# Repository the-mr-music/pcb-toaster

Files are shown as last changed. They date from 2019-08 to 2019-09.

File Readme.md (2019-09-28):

# PCB Toaster



> **WARNING:** This project is dealing with 230VAC. You have to take safety preautions and provide proper isolation. Never touch the mains side of the circuit if power is applied. If you are not experienced in high voltage electronics do not attempt to build this circuit. I do take NO WARRANTY or LIABILITY for any damages when building or operating this device.

## Introduction

In my spare time I have been doing quite a lot of PCBs over the years. Starting with SMD sizes of 1206, with increasing circuit complexity I started using smaller and smaller component sizes. From 1206 over 0805, now ending up at 0402 and my first stenciling "adventures". Whilst browsing Instagram, I stumbled upon [Maker Moekoe's Hot Plate Reflow Iron](https://github.com/makermoekoe/Hotplate-Soldering-Iron), from which I grabbed a bit of inspiration for this quite similar project. As I did not have any spare parts lying around and wanted to do something with higher voltages anyway, I decided to build an all-in-one PCB.
(Fun fact - it is not actually a toaster)

## Roadmap

This current project is still work in progress. Be sure to check back later when it's finished.

- [x] Get an iron and disassemble it
- [x] Do all the calculations on the power side
- [x] Component selection
- [x] Design and order the PCB
- [x] Build and test the PCB
- [x] Plan the case and mounting, get materials
- [x] Take a nap
- [x] PCBs arrive 
- [x] Build and wire everything
- [x] Read up theoretical information about reflow soldering and solder paste
- [x] Program a first firmware version (curious if PID regulator will be necessary or a plain two-point regulator is sufficient)
- [ ] Refine the firmware

## PCB Design Notes

### Primary Side

Having only done one pcb incorporating 230 VAC and low voltage (before always used old 5 V phone chargers or other PSUs), but on serparate pcbs, I wanted to opt for an all-on-one pcb design. At LCSC.com I found an affordable print switching PSU ([GTL-POWER-VB02](https://datasheet.lcsc.com/szlcsc/1811211452_GTL-POWER-VB02-T2S03_C335526.pdf)), with an output of 3.3 V at 500 mA, which seemed perfect for the job. Their datasheet (at least the parts I could understand with the help of translator) recommended additional filtering at the output, which has been followed by me. Regarding the primary side, either a simple approach consisting out of a fuse, a varistor and a current limiting resistor or a more EMV saving pre-circuit is possible. As this device is just occasionally in use, the protective circuit is good enough for me.

Regarding the power switch for the iron itself, a BT-138 is used. Primarily because I already had this type of TRIAC already in use together with a MOC3083 and know it's working well together. The resistor values are taken from the MOC's datasheet. Because the SMD resistors have a maximum voltage rating of 250 V, I put two of them in series. All of the tracks carrying the heavy load are approximately five millimeters wide, but run on two layers. As a result a current of in total 10 A is achievable, which is limited by the fuse F1. For ease of layouting, the psu (on fuse F2) and iron are sharing F1. As the iron I use has a cold resistance of 42 Ohms, a 6.3 Ampere fuse is sufficient for F1.

The isolation between any track or plane of different nets is at least five millimeters, depending on the necessity I may also apply a thin layer of spray varnish. To protect against touch, the whole pcb will be mounted behind a sheet of plexiglass.

### Secondary Side

#### Controller

Both controller and peripherals are running at 3.3 V. I decided to connect Earth and GND together (at the cost of more EMV). For someone not wanting this, it is possible to just not fit the resistor R21. In contrast to the primary side, the spacing between Earth and GND is not five, but only three millimeters.

The brain of the circuit is an STM32F103 microcontroller in a small QFN package running at a maximum of 72 MHz. Although way to powerful for the application, it has the advantage to be compatible with the Arduino IDE, so others have an easier time programming their own firmware.
The USB interface of the controller has not been broken out onto the pcb. Any firmware can be flashed by using the SWD interface or the bootloader on the STM32, both accessible through the debug pin socket at the bottom. To activate the bootloader, keep the button pressed and reset the device.
I will be sticking to plain C and the STM32 HAL layer though, more to that in the firmware section.

For temperature measurement I use the MAX6675 thermocouple measurement IC that is connected via SPI to the STM32. The opto triac to turn on the iron is connected to an I/O and has an indicator LED (iron logo) in parallel.

#### User Interaction

The user in total can interact with the device over one push button, one potentiometer, an OLED display and three LEDs.

To set the desired temperature, a potentiometer will be used and read out by the microcontrollers ADC. The AVCC pins have not gotten any additional filtering, as the potentiometer used is just for roughly setting the temperature. Although the STM32 provides a 12 bit ADC, only eight bit are necessary and I will just average a few measurements in the firmware.
For starting or interrupting the heating process the button is used. One can fit a push button directly on the pcb or connect a cable to a button mounted in the plexiglass panel.

To give the user feedback, a small 128x64 px OLED (displays the current temperature, soldering time, etc...) is connected to the STM32 over SPI. Because there were a few spare I/Os left on the controller, I added three more LEDs that can be turned on or off by the firmware.

### PCB Renders

The PCB renders have been created using Greg Davill's KiCAD Script. Order was placed at JLCPCB as I still had other PCBs to be made. First image is the top, second the bot view.

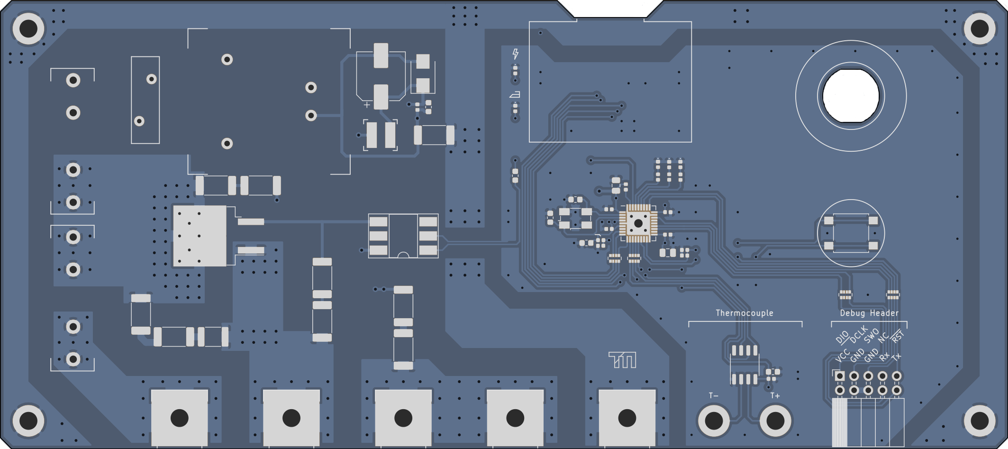
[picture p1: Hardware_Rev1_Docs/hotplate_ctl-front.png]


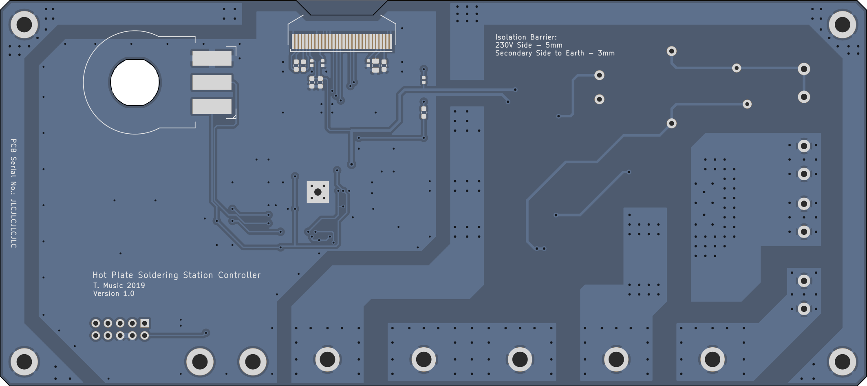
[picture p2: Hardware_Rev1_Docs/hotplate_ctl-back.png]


## Simulation

After the PCB has been sent to the fab, I was curious which performance to expect and decided to coarsely model the hot plate in python.
Even though the script is a bit chaotic and is using really coarse values, the result is surprisingly accurate. Those who are interested and have numpy and matplotlib installed can have a look at the Simulation folder.

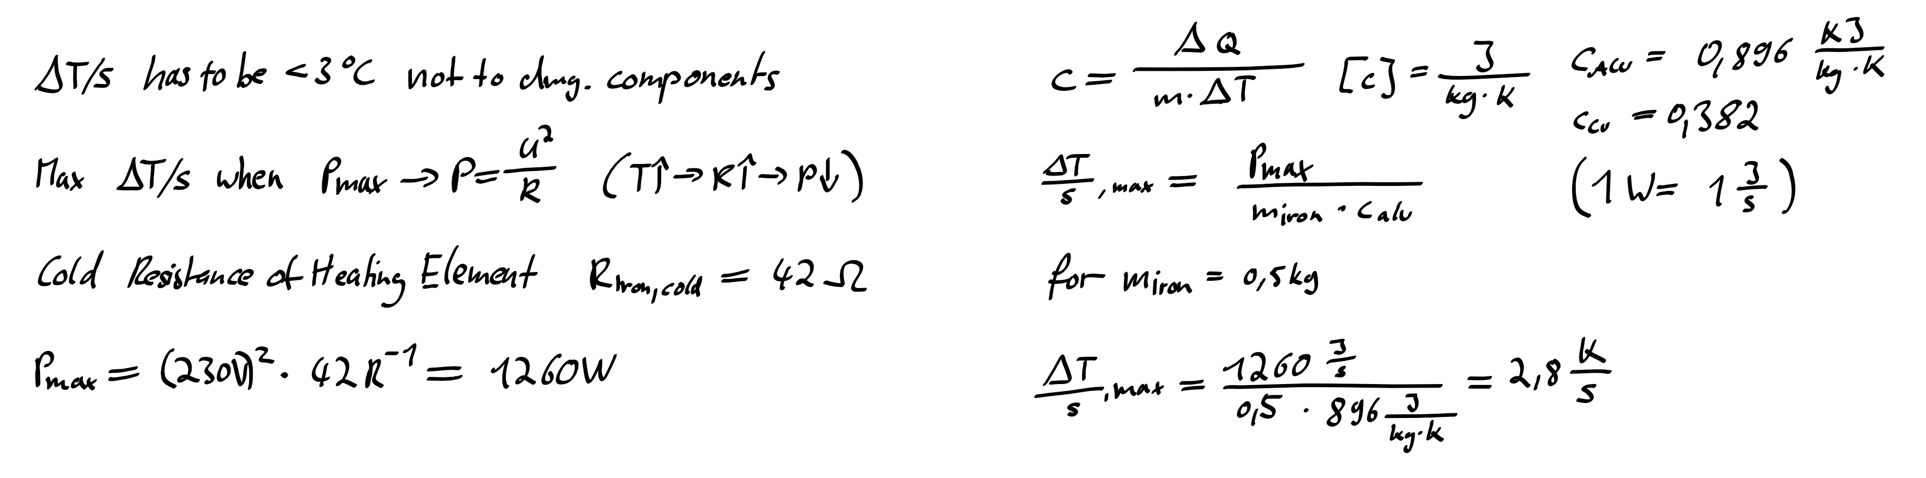
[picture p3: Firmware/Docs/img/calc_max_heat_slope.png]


### PCB Assembly
The soldering itself went quickly, however I can not really recommend the 0402 resistor networks without a stencil. As the components came from LCSC and these were missing in KiCAD, I drew the footprints of the potentiometer, PSU, fuse holders, as well as the OLED and everything fit like a charm.

## Mounting
In order to prevent the terminals from being touched, an acrylic glass will be mounted on top of it. Two cutouts for the potentiometer and button are made.

The plate itself get really hot and should neither damage the base plate (in case of wood) or steal the heat (in case of metal). As solution it is mounted on a piece of FR4, which is in turn screwed to the base plate.

However I still have not decided if I will make the case out of wood or metal. Until the device is fully finished, the PCB is in a plastic box to prevent touching from the bottom and the Iron is mounted on a wooden plate.

## Firmware
With the hardware done, up to the firmware. 

### Libraries used
For easier scheduling and extensibility I chose to deploy a freeRTOS on the device in conjunction with the STM32 HAL libraries. Then the really good u8g2 library by Oli Kraus for controlling the OLED and finally an own implementation of Brett Beauregard's well working PID controller.

### Iron Power Control

Wave packet control. Prescaler of 8000 @ 64 MHz core clock. Timer in PWM mode with 8000 period -> 1 second. One half wave is 10 ms. error is x

Simulation results show a maximum temperature increase per second of around 2,5 °C. This is below the allowed 3 °C increase per second. When heating the iron with maximum power, it is

As the power of the plate is not high enough support the accurate temperature profile, I will try to take a different approach. At first preheat with maximum heat to 100 °C, at which point the flux starts activating. After the flux is active, the whole soldering process should be completed in three minutes. A PID regulator will then take care of regulating it to the peak temperature.

### Tasks
The first task deals with reading out and preprocessing the thermocouple temperature. The MAX6675 in worst case needs 225ms for one conversion. With SPI at 4 MHz one can achieve four temperature readings in one second. If the value passes the sanity check, it is added to a ringbuffer. This way always the last four temperature readings get averaged providing a stable temperature reading once per second, matching our PID regulator's calculation interval.

The second task is 

control task. Oled, logging and 

pid task. PID regulator based on brett beauregards code.

Currently only one temperature curve is programmed for the Chipquik TS391AX50 (Sn63/PB37, TAL@183 °C). The potentiometer is 

<p>&copy; T. Music 2019<br/>This work is licensed under CC BY-SA 4.0 (https://creativecommons.org/licenses/by-sa/4.0/legalcode)</p>

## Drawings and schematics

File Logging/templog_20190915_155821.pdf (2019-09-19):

## Temperature Curve Measurement 16:03 - 15.09.2019 kp: 4.270 ki: 0.100 kd: 35.400

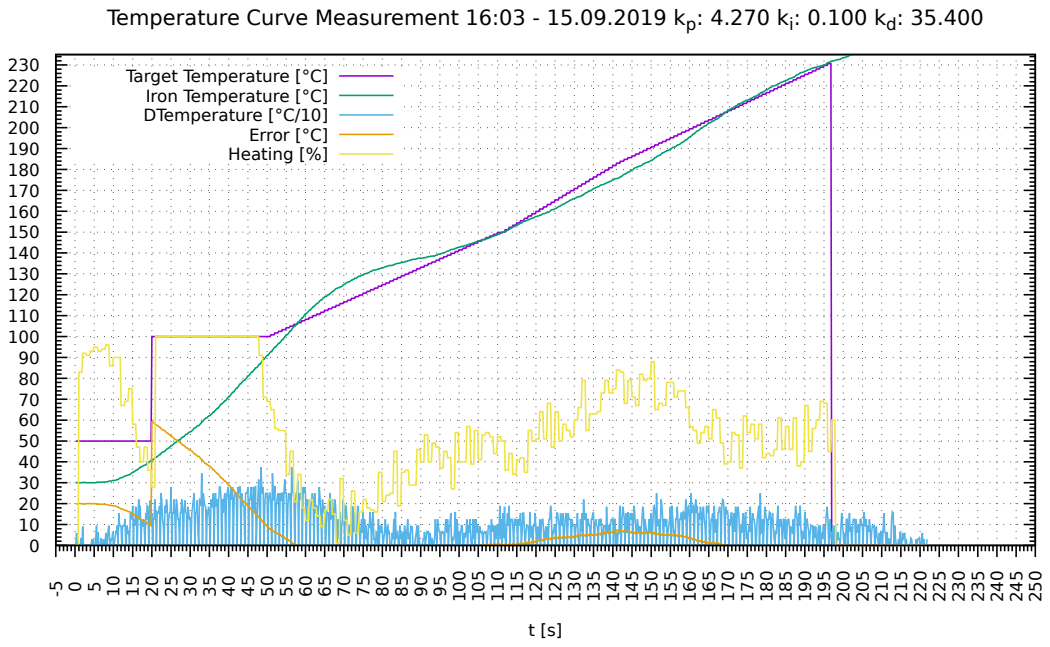
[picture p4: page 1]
Target Temperature [°C] Iron Temperature [°C] DTemperature [°C/10] Error [°C] Heating [%]

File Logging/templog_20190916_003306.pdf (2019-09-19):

## Temperature Curve Measurement 00:38 - 16.09.2019 kp: 4.270 ki: 0.100 kd: 35.400

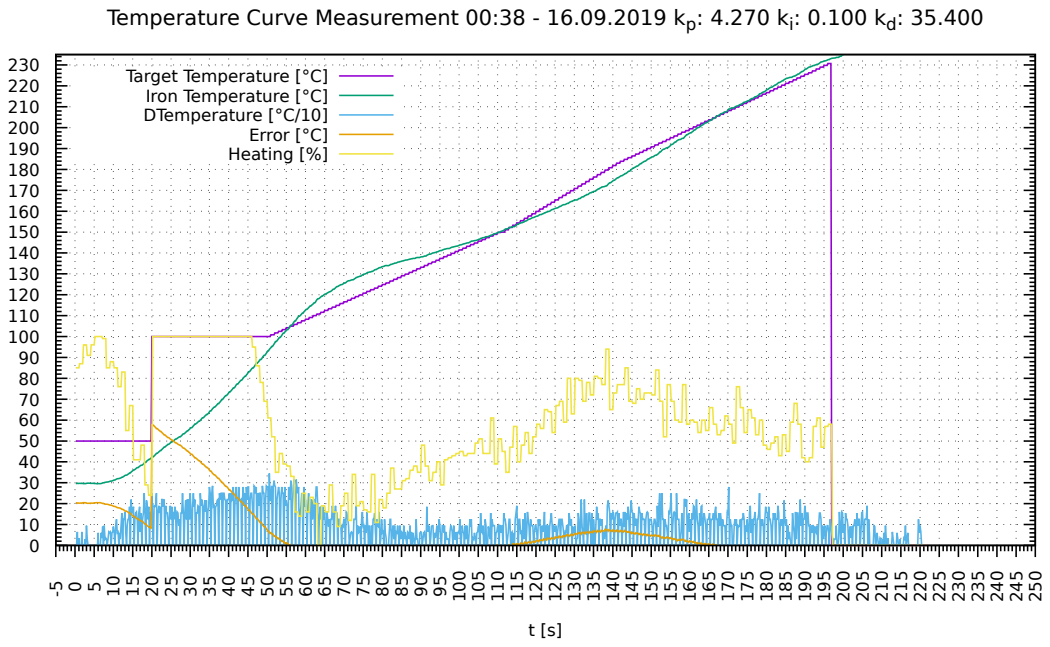
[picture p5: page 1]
Target Temperature [°C] Iron Temperature [°C] DTemperature [°C/10] Error [°C] Heating [%]

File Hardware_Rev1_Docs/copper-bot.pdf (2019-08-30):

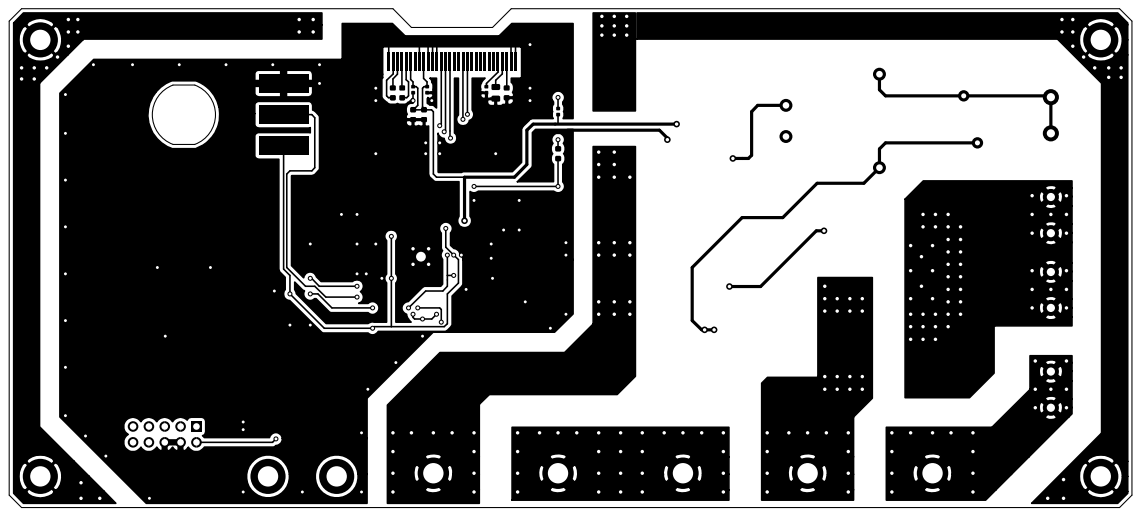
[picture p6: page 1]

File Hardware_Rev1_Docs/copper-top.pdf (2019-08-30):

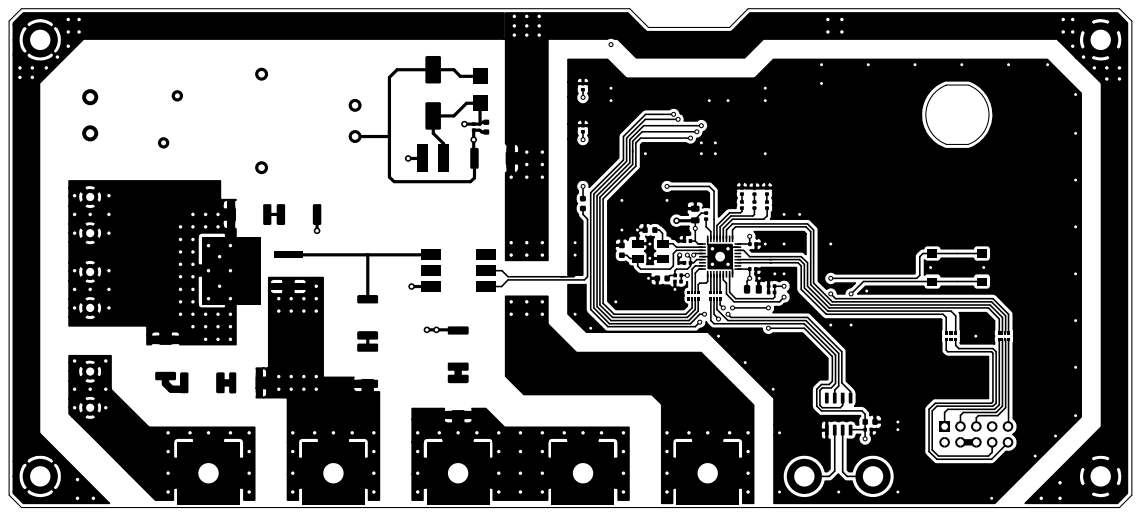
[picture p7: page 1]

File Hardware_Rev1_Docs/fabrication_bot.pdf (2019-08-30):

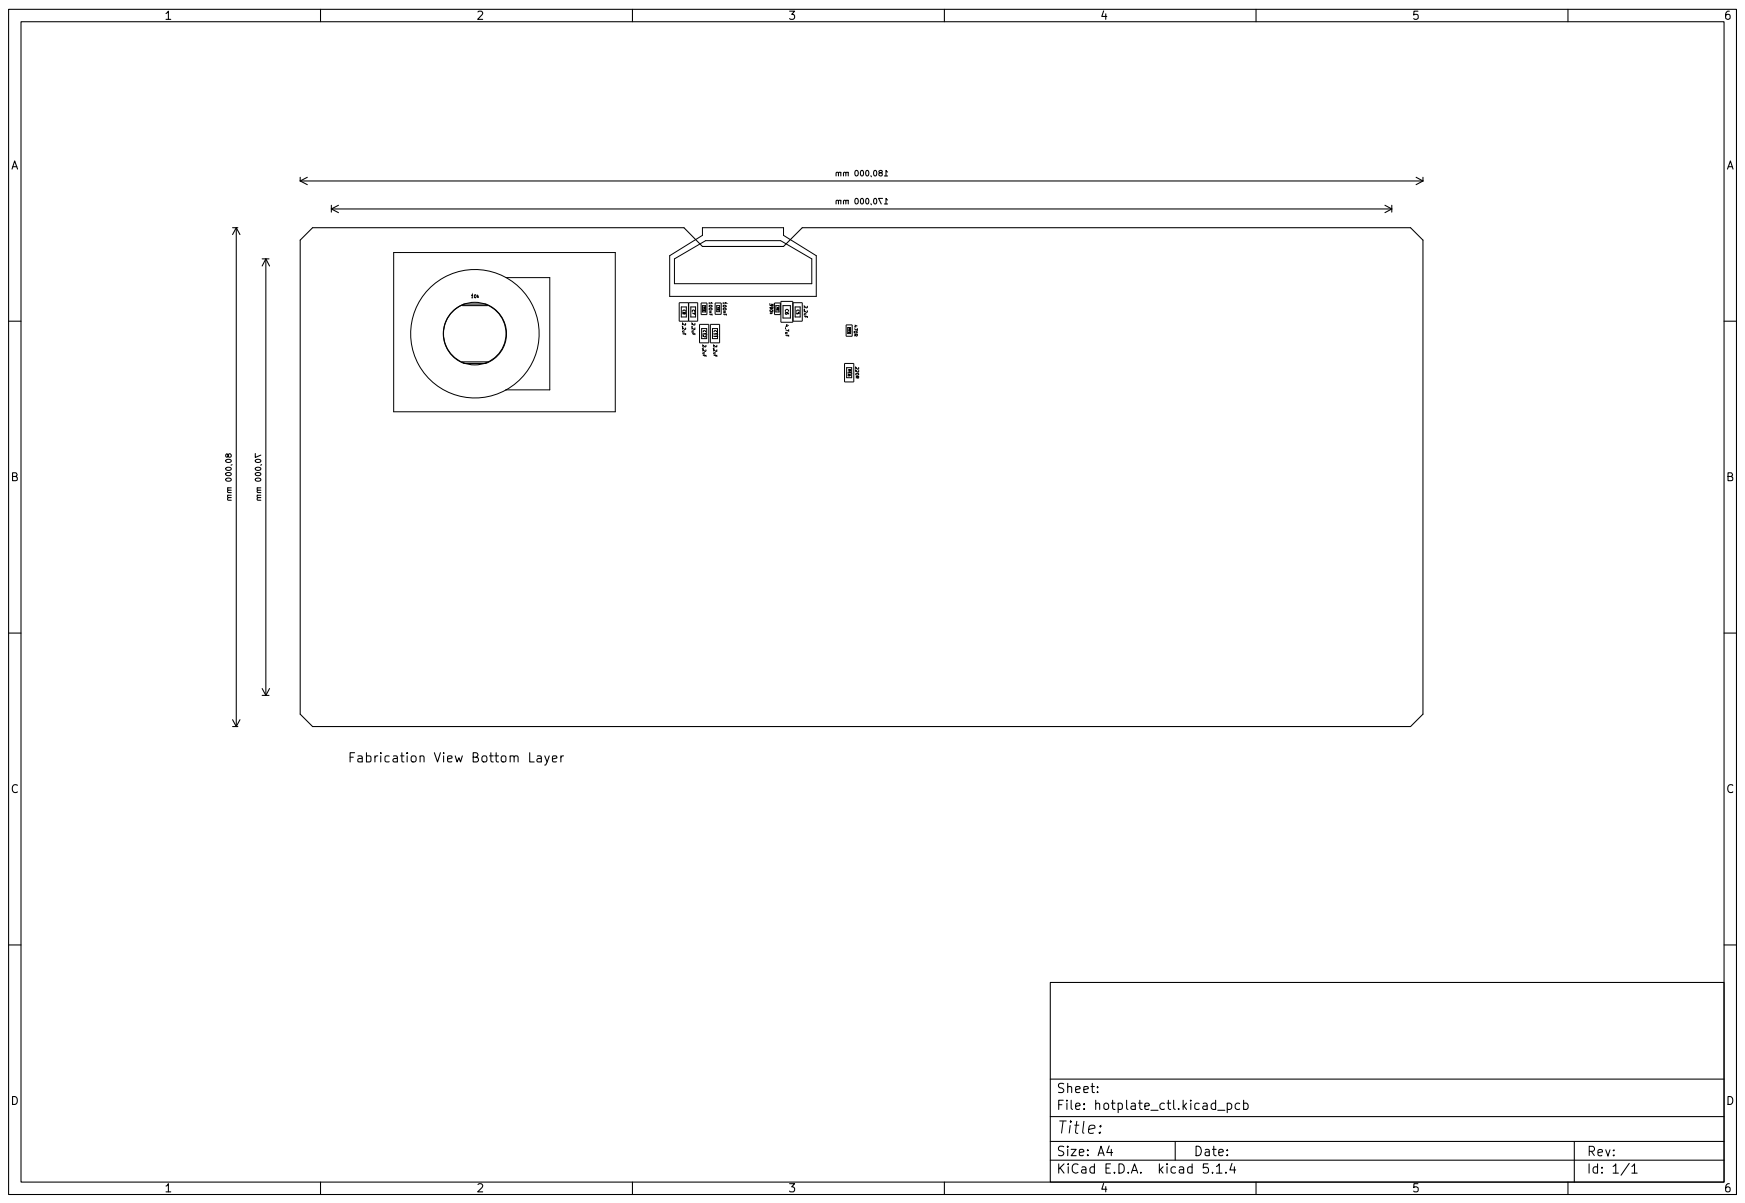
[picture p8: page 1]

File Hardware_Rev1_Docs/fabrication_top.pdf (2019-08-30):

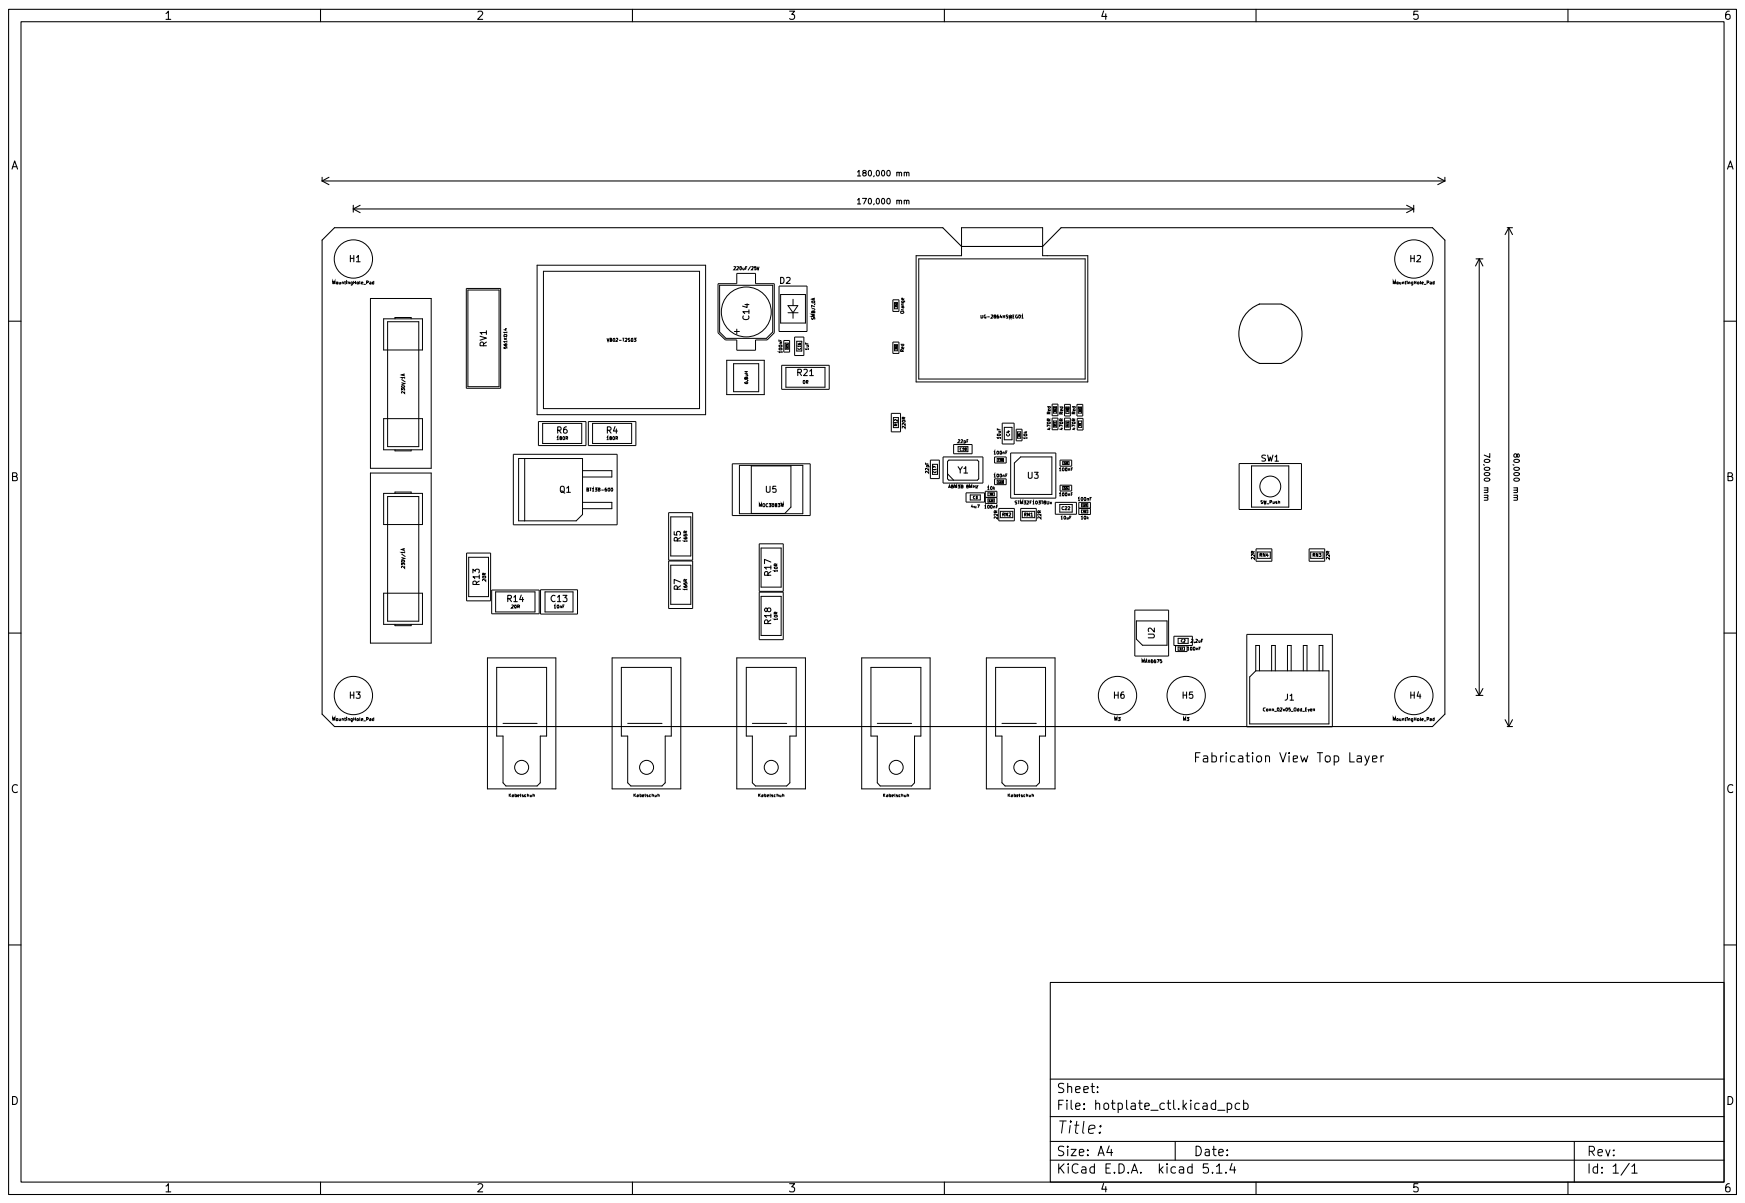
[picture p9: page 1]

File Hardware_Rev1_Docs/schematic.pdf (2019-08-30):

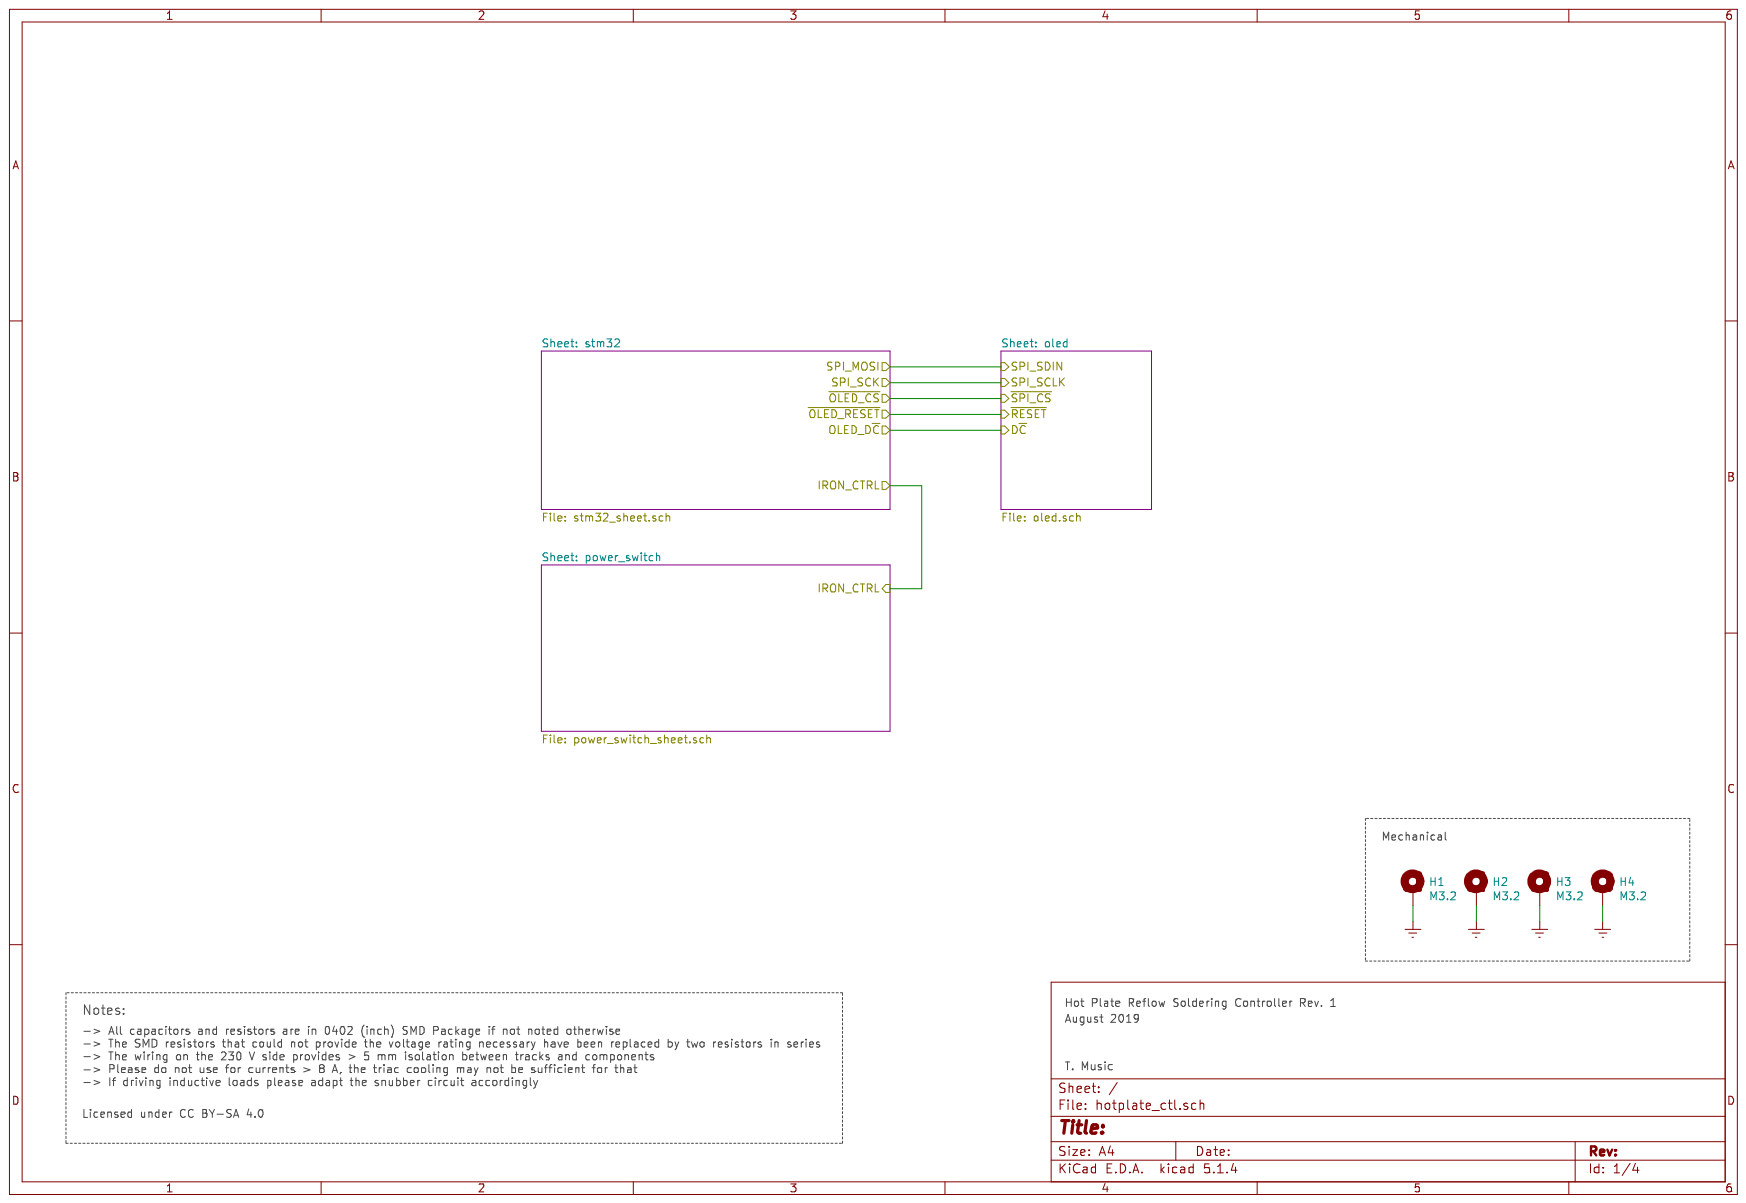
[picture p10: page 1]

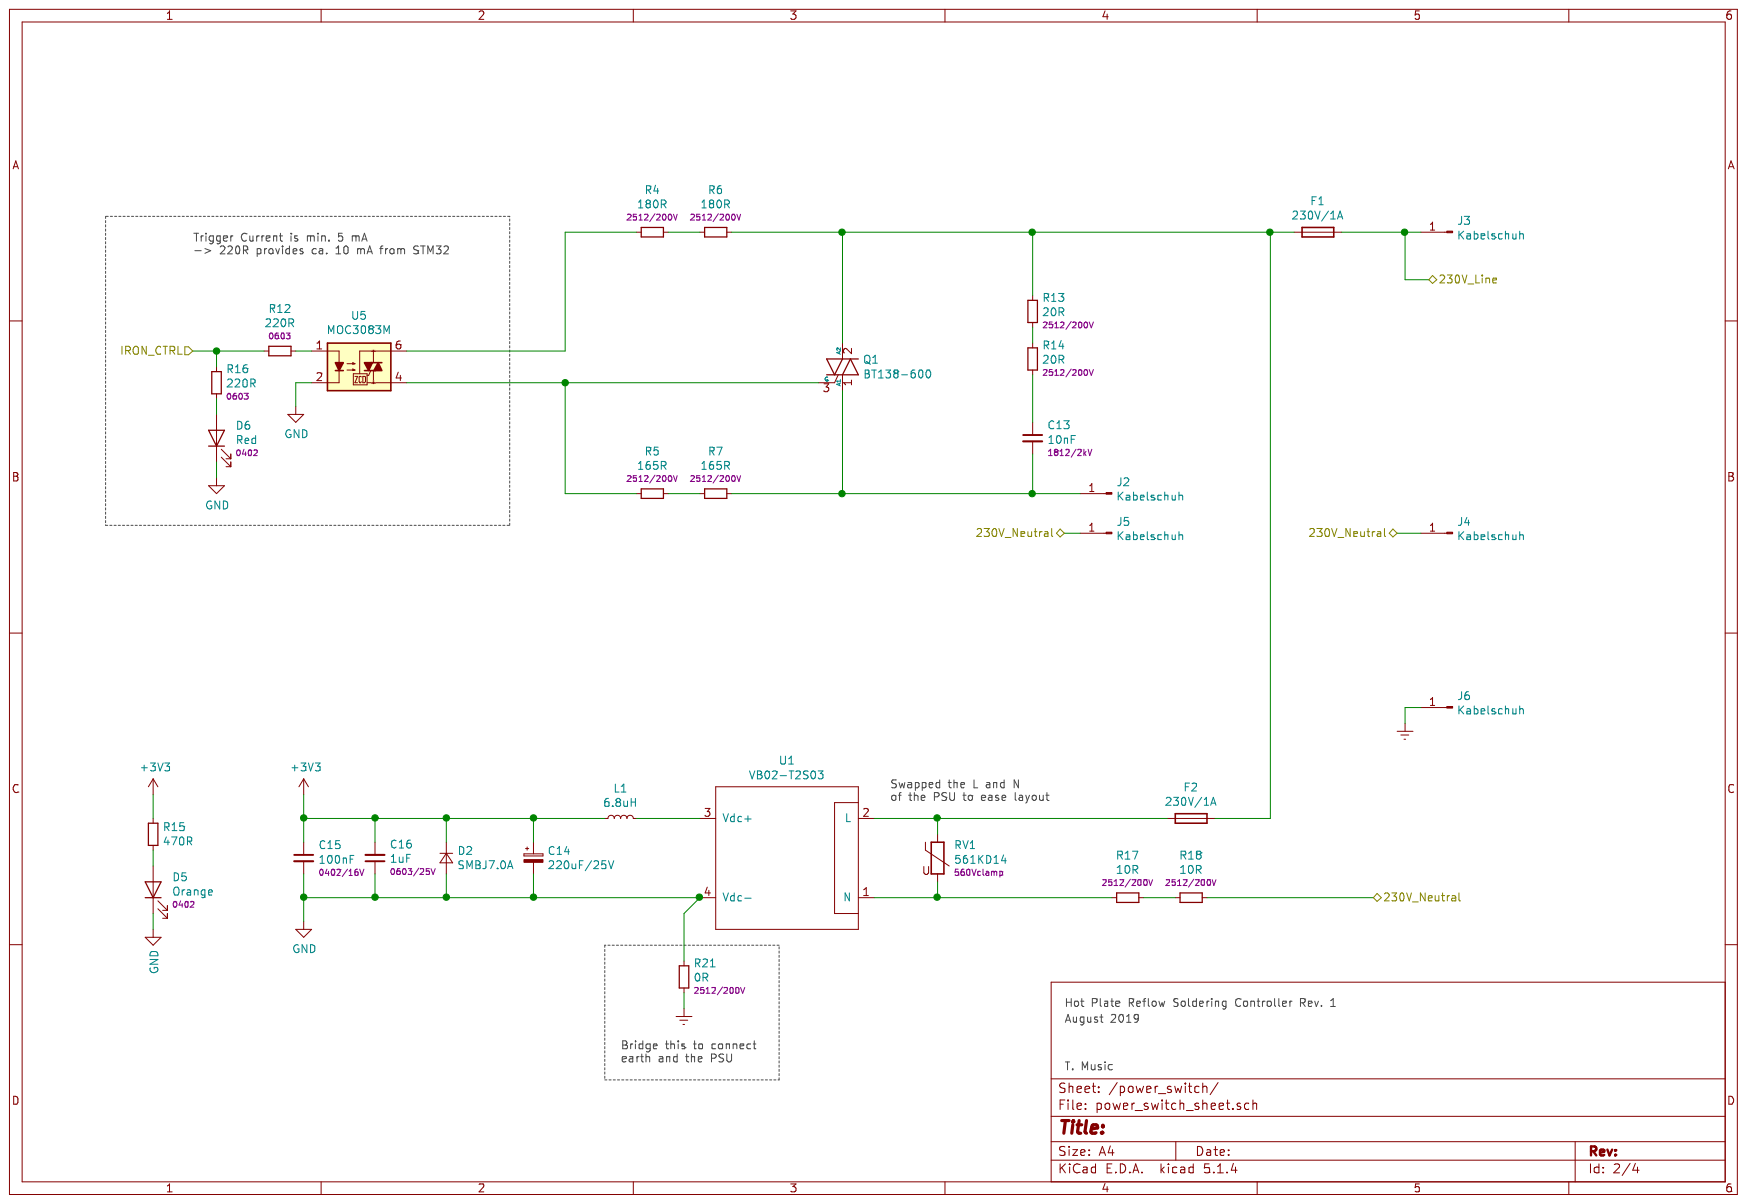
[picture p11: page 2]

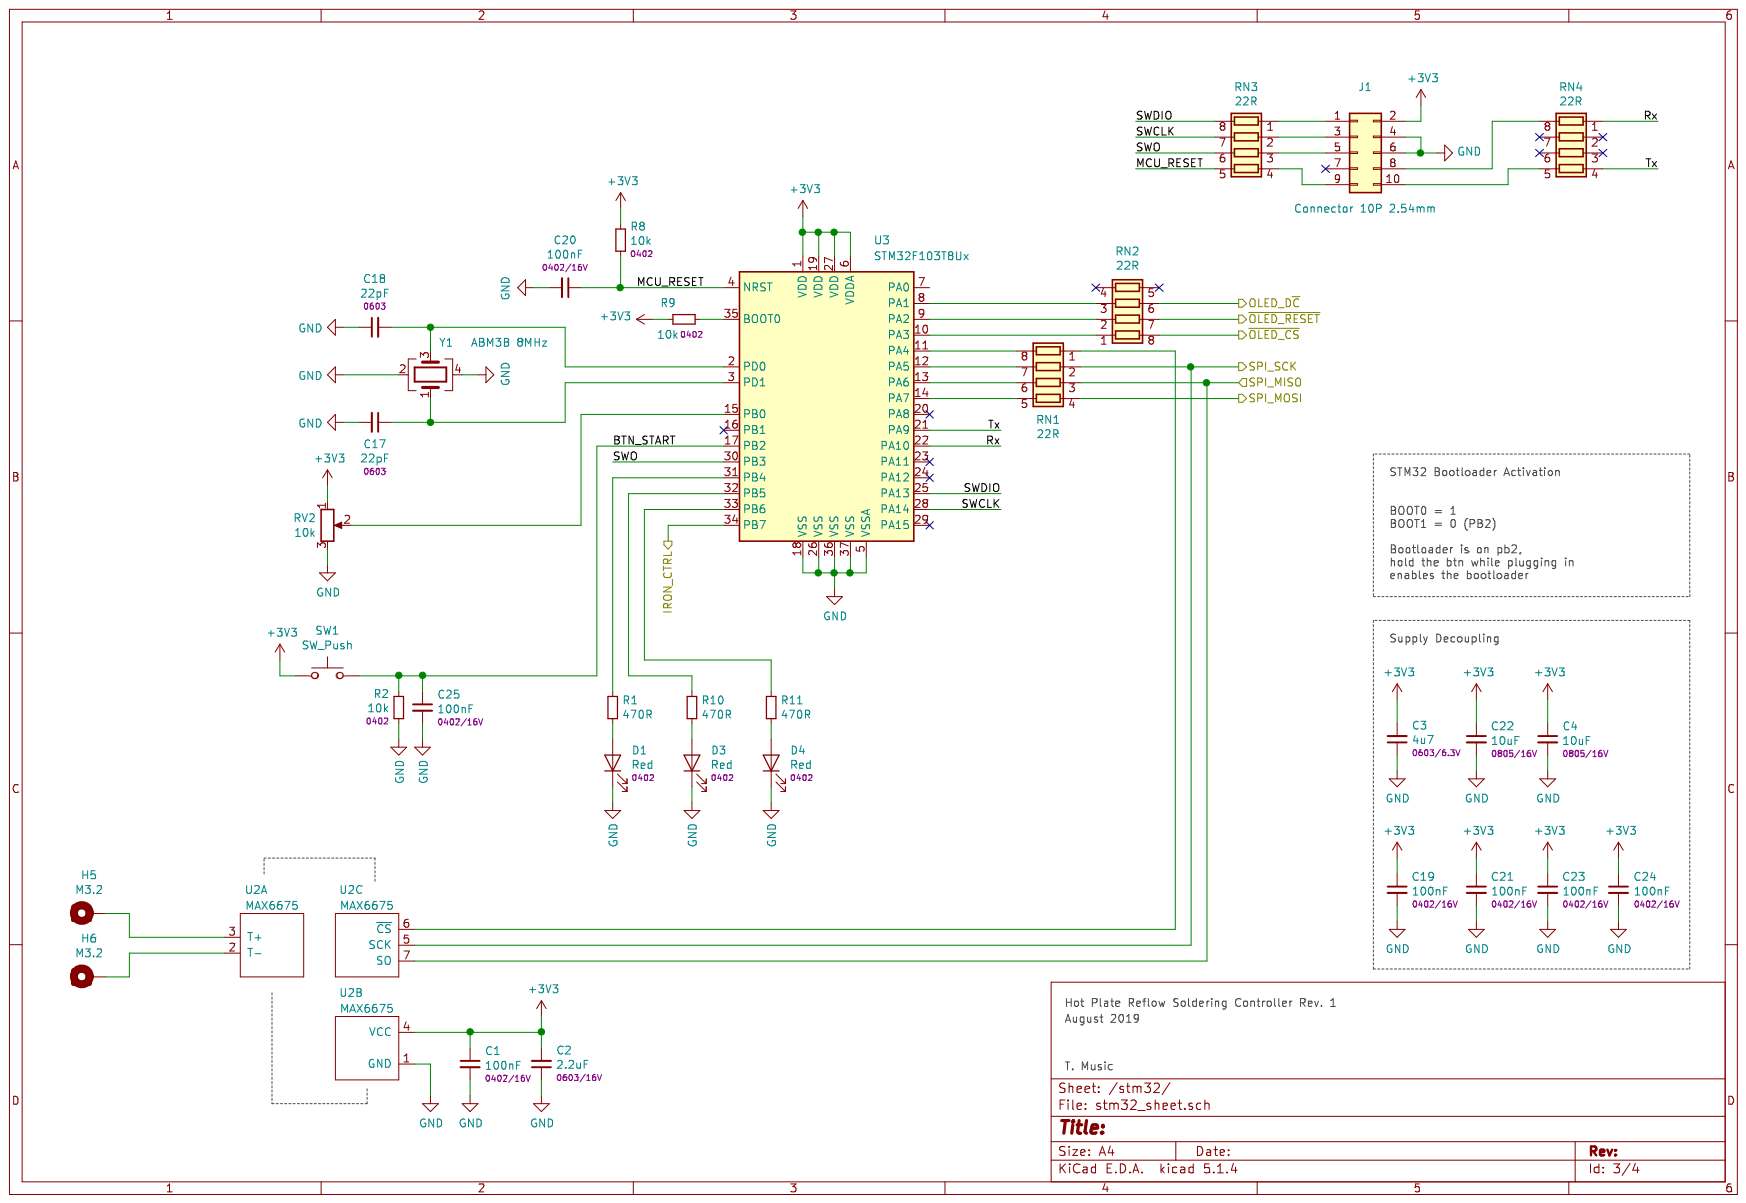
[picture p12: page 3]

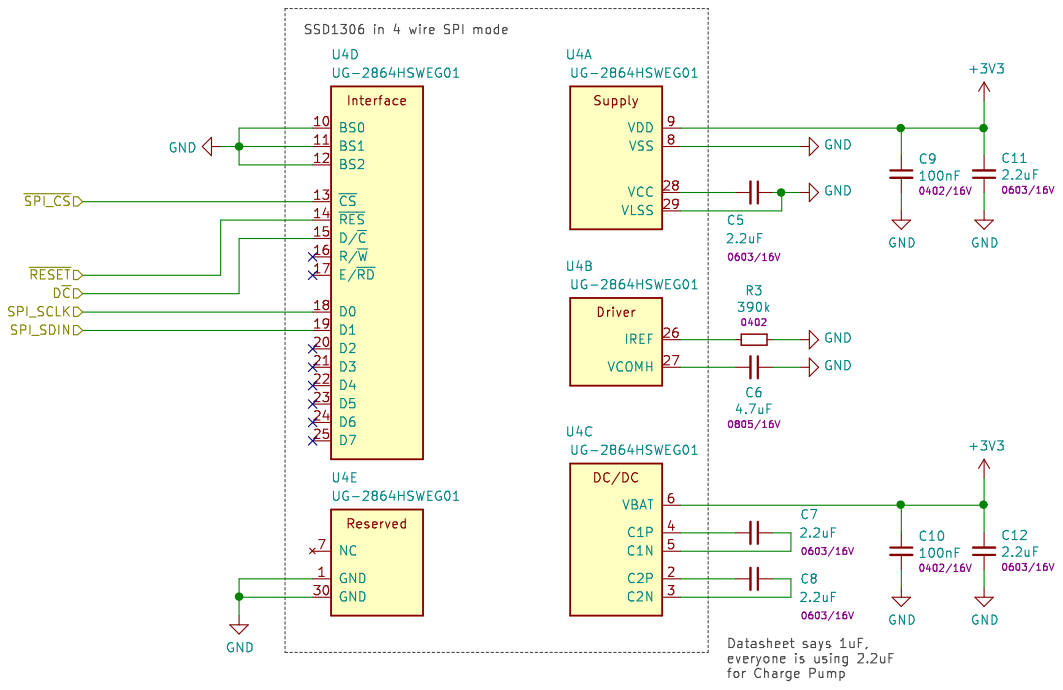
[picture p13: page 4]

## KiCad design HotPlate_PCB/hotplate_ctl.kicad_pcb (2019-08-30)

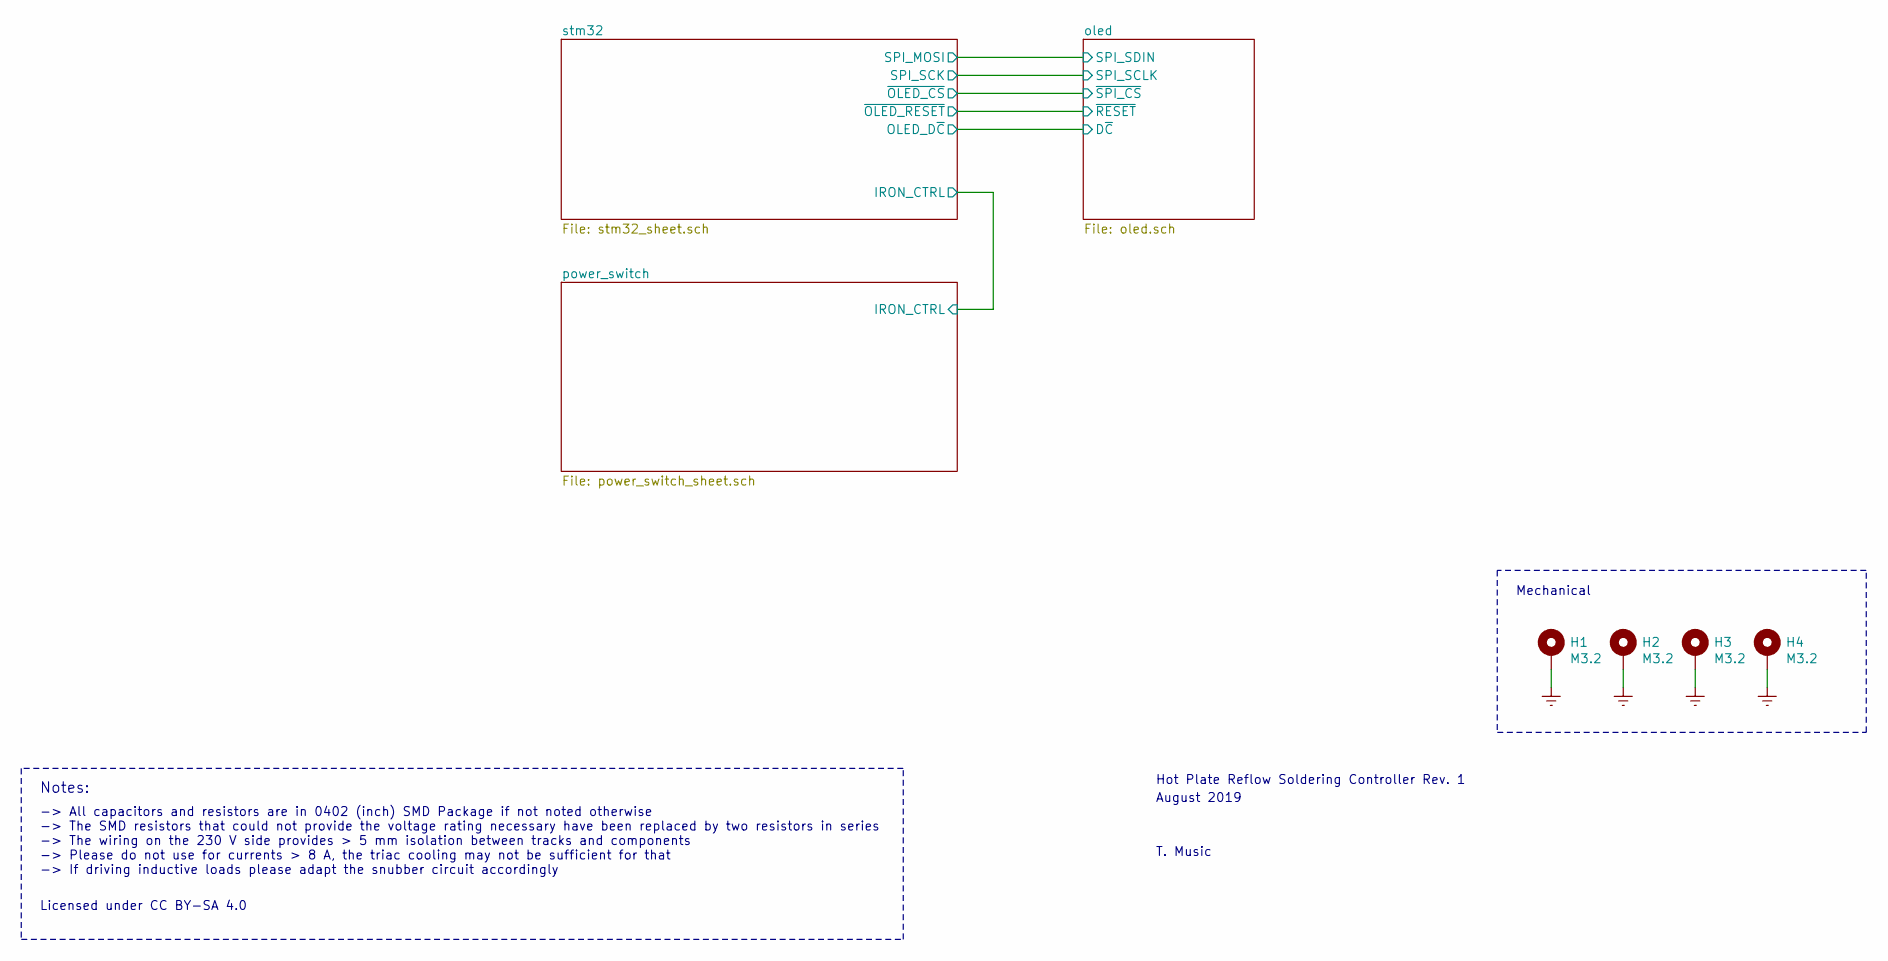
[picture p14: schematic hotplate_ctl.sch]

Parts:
H1, H2, H3, H4: M3.2; MountingHole_3.2mm_M3_DIN965_Pad

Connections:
Earth: H1.1, H2.1, H3.1, H4.1; also elsewhere on the board

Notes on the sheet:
Hot Plate Reflow Soldering Controller Rev. 1
August 2019
T. Music
-> All capacitors and resistors are in 0402 (inch) SMD Package if not noted otherwise -> The SMD resistors that could not provide the voltage rating necessary have been replaced by two resistors in series -> The wiring on the 230 V side provides > 5 mm isolation between tracks and components -> Ple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
Notes:
Licensed under CC BY-SA 4.0
Mechanical

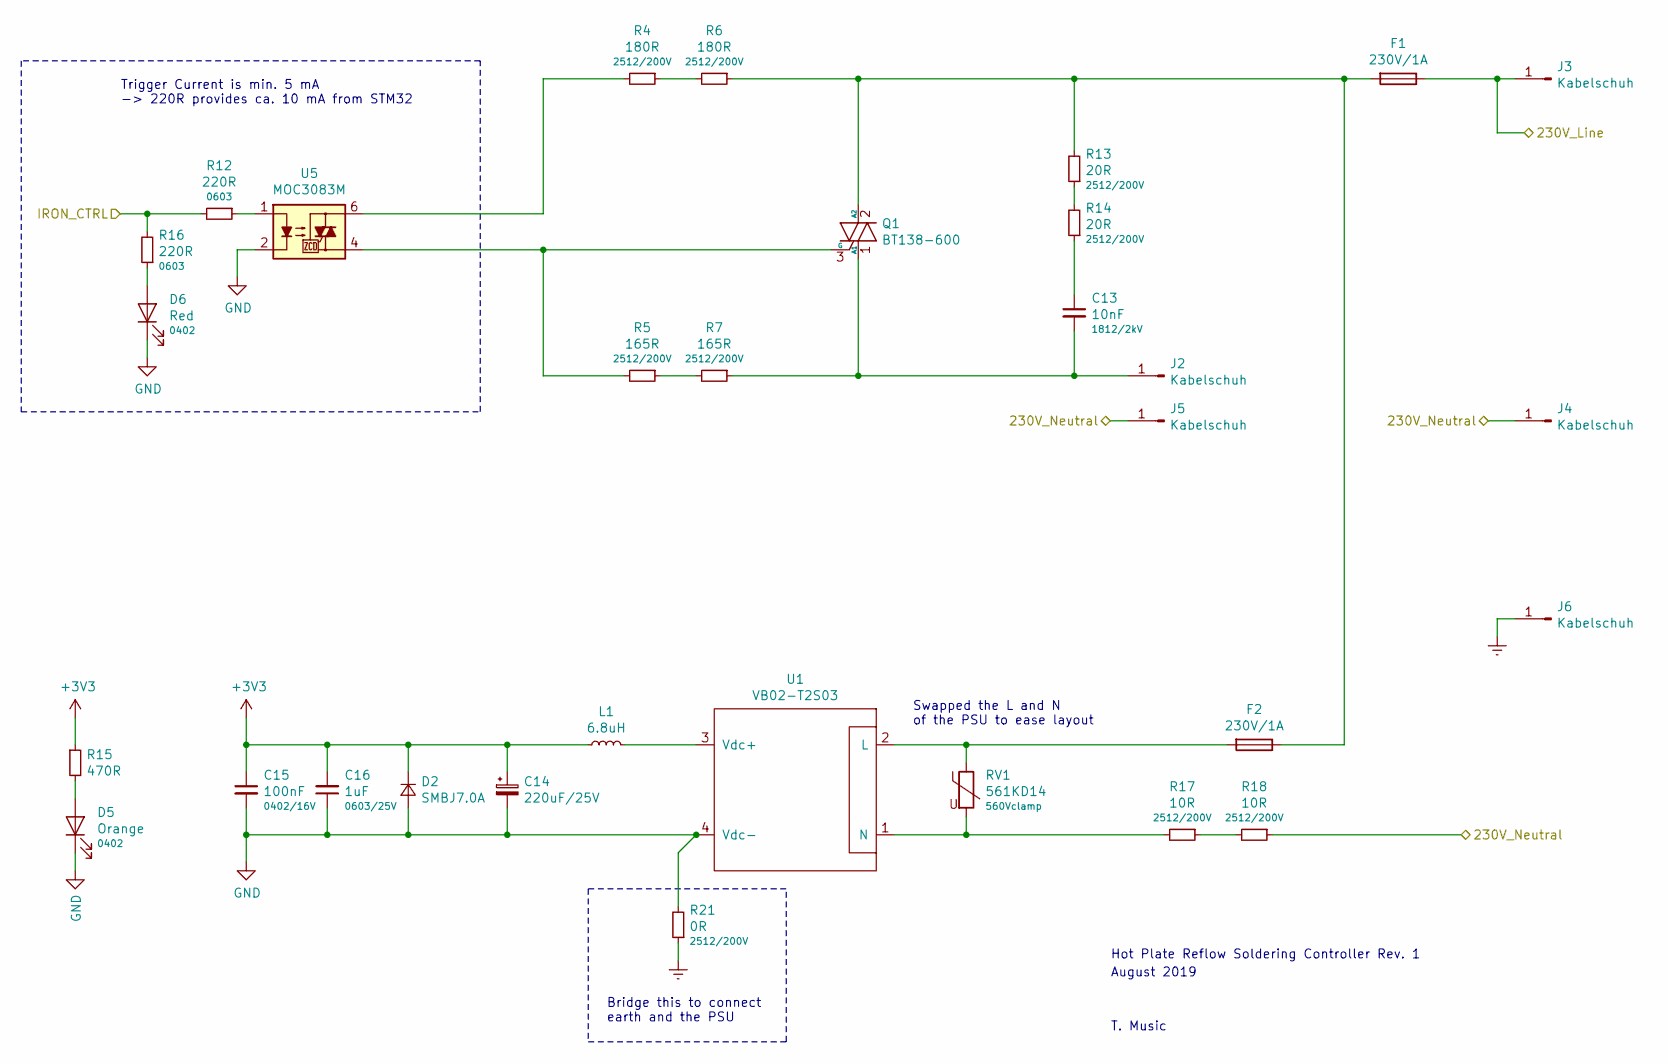
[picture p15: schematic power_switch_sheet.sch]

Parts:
C13: 10nF; C_1812_4532Metric
C14: 220uF/25V; CP_Elec_8x10.5
C15: 100nF; C_0402_1005Metric; Rating 0402/16V
C16: 1uF; C_0603_1608Metric; Rating 0603/25V; LCSC C23630
D2: SMBJ7.0A; D_SMB
D5: Orange; LED_0402_1005Metric; Rating 0402
D6: Red; LED_0402_1005Metric; Rating 0402
F1, F2: 230V/1A; XC-Elec-C3130
J2, J3, J4, J5, J6: Kabelschuh; kabelschuh_horizontal_8x19mm
L1: 6.8uH; SM4532
Q1: BT138-600; TO-263-2
R4, R6: 180R; R_2512_6332Metric; Rating 2512/200V
R5, R7: 165R; R_2512_6332Metric; Rating 2512/200V
R12, R16: 220R; R_0603_1608Metric; Rating 0603
R13, R14: 20R; R_2512_6332Metric; Rating 2512/200V
R15: 470R; R_0402_1005Metric
R17, R18: 10R; R_2512_6332Metric; Rating 2512/200V
R21: 0R; R_2512_6332Metric; Rating 2512/200V
RV1: 561KD14; RV_Disc_D15.5mm_W5mm_P7.5mm; Rating 560Vclamp
U1: VB02-T2S03; VB02-T2Sxx
U5: MOC3083M; DIP-6_W8.89mm_SMDSocket_LongPads

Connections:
+3V3: C14.1, C15.1, C16.2, D2.1 (K), L1.1, R15.1; also elsewhere on the board
/power_switch/230V_Line: F1.1, J3.1
/power_switch/230V_Neutral: J4.1, J5.1, R18.1
/power_switch/IRON_CTRL: R12.2, R16.2; also elsewhere on the board
Earth: J6.1, R21.1; also elsewhere on the board
GND: C14.2, C15.2, C16.1, D2.2 (A), D5.1 (K), D6.1 (K), R21.2, U1.4 (Vdc-), U5.2; also elsewhere on the board
unnamed: C13.1, R14.1
unnamed: C13.2, J2.1, Q1.1 (A1), R7.1
unnamed: D5.2 (A), R15.2
unnamed: D6.2 (A), R16.1
unnamed: F1.2, F2.1, Q1.2 (A2), R6.1, R13.2
unnamed: F2.2, RV1.1, U1.2 (L)
unnamed: L1.2, U1.3 (Vdc+)
unnamed: Q1.3 (G), R5.2, U5.4
unnamed: R4.1, R6.2
unnamed: R4.2, U5.6
unnamed: R5.1, R7.2
unnamed: R12.1, U5.1
unnamed: R13.1, R14.2
unnamed: R17.1, R18.2
unnamed: R17.2, RV1.2, U1.1 (N)

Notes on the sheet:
Trigger Current is min. 5 mA -> 220R provides ca. 10 mA from STM32
Bridge this to connect earth and the PSU
Swapped the L and N of the PSU to ease layout
Hot Plate Reflow Soldering Controller Rev. 1
August 2019
T. Music

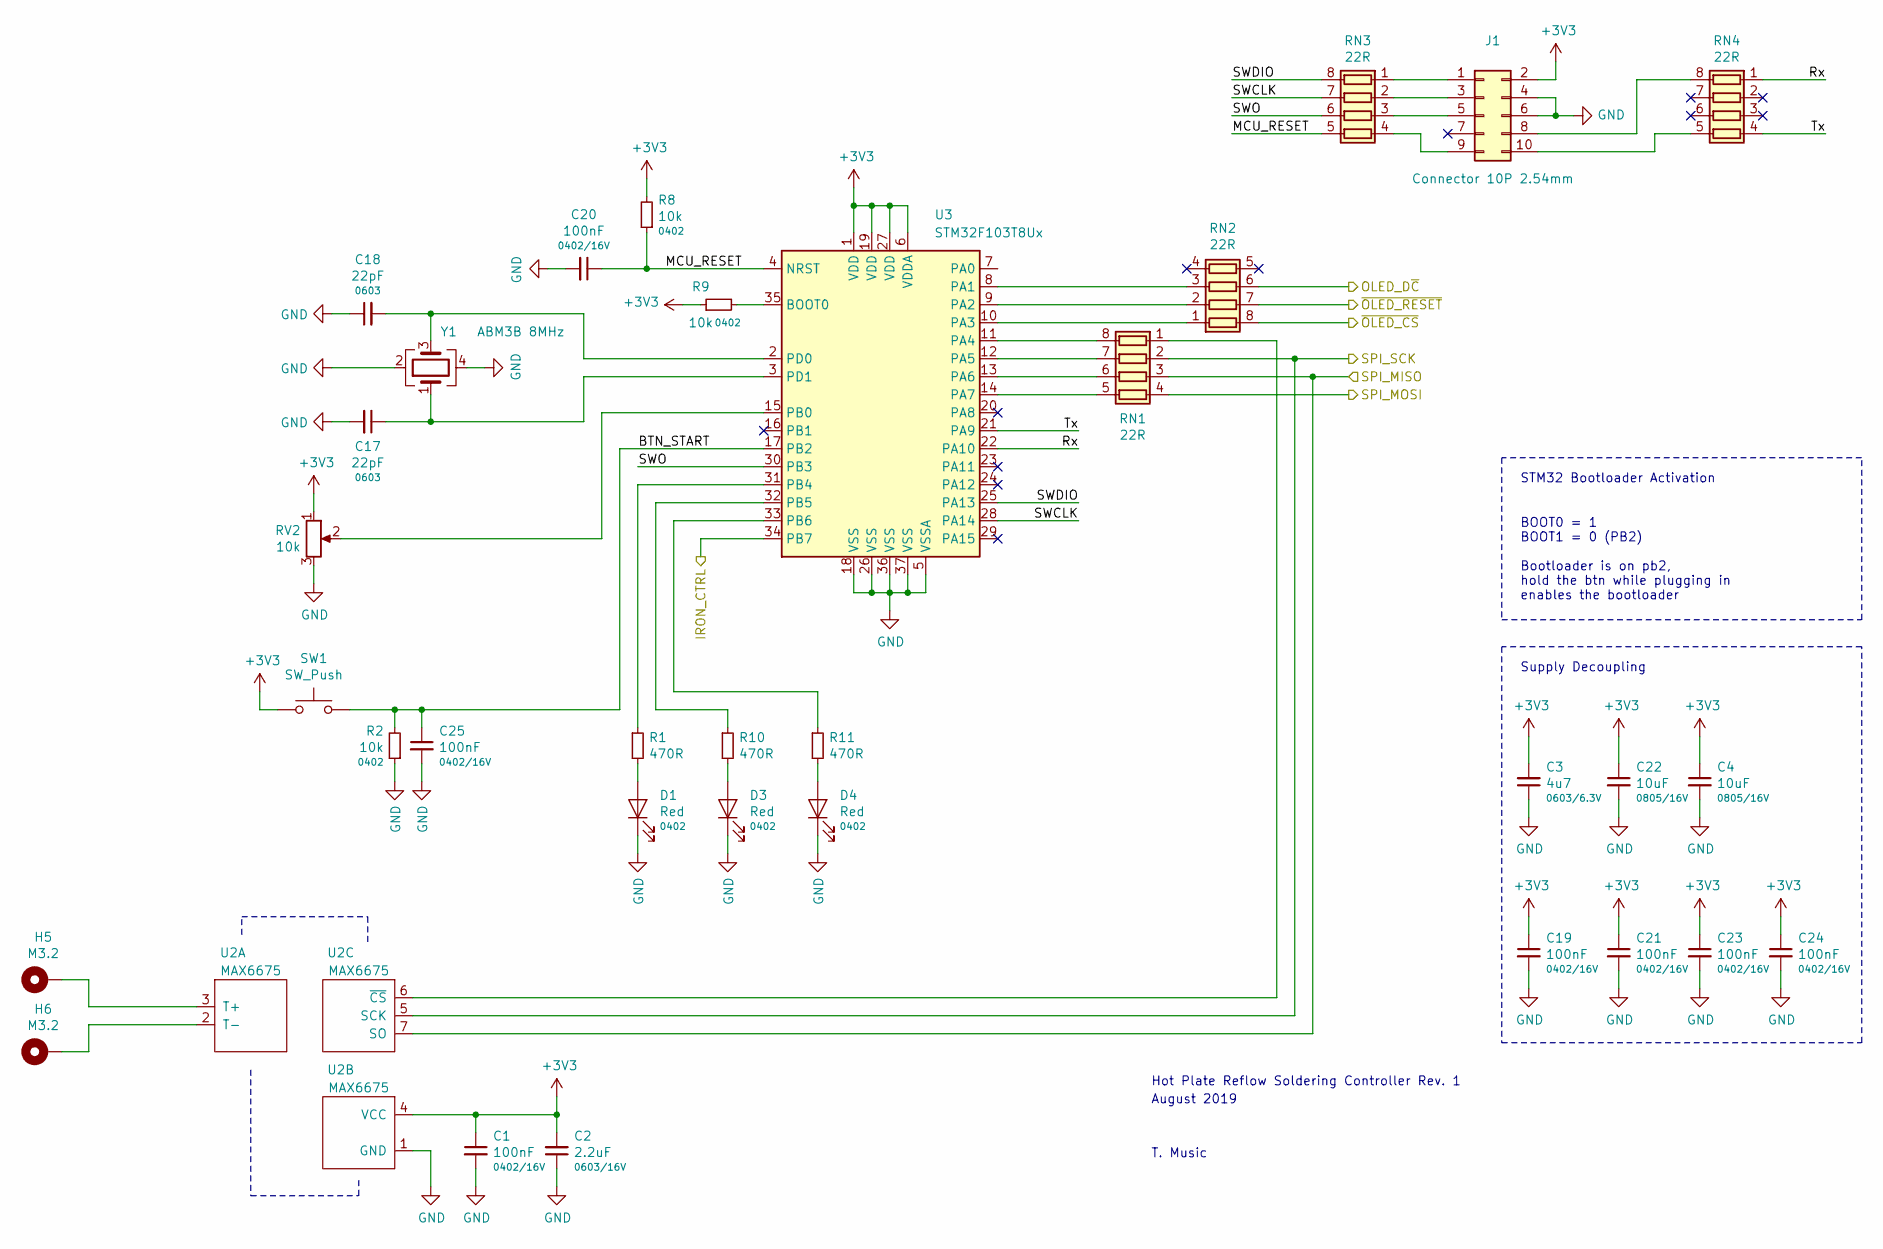
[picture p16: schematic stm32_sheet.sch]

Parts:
C1, C19, C20, C21, C23, C24, C25: 100nF; C_0402_1005Metric; Rating 0402/16V
C2: 2.2uF; C_0603_1608Metric; Rating 0603/16V; LCSC C23630
C3: 4u7; C_0603_1608Metric; Rating 0603/6.3V
C4, C22: 10uF; C_0805_2012Metric; Rating 0805/16V
C17, C18: 22pF; C_0603_1608Metric; Rating 0603
D1, D3, D4: Red; LED_0402_1005Metric; Rating 0402
H5, H6: M3.2; MountingHole_3.2mm_M3_DIN965_Pad
J1: Connector 10P 2.54mm; PinSocket_2x05_P2.54mm_Horizontal
R1, R10, R11: 470R; R_0402_1005Metric
R2, R8, R9: 10k; R_0402_1005Metric; Rating 0402
RN1, RN2, RN3, RN4: 22R; R_Array_Convex_4x0402
RV2: 10k; Potentiometer_Hole_10mm
SW1: SW_Push; SW_SPST_B3S-1000
U2: MAX6675; SO-8_3.9x4.9mm_P1.27mm
U3: STM32F103T8Ux; QFN-36-1EP_6x6mm_P0.5mm_EP4.1x4.1mm
Y1: ABM3B 8MHz; Crystal_SMD_Abracon_ABM3B-4Pin_5.0x3.2mm

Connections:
+3V3: C1.1, C2.2, C3.2, C4.1, C19.1, C21.1, C22.1, C23.1, C24.1, J1.2, R8.2, R9.1, RV2.1, SW1.1, U2.4 (VCC), U3.1 (VDD), U3.6 (VDDA), U3.19 (VDD), U3.27 (VDD); also elsewhere on the board
/oled/D~C: RN2.6 (R3.2); also elsewhere on the board
/power_switch/IRON_CTRL: U3.34 (PB7); also elsewhere on the board
/stm32/BTN_START: C25.1, R2.2, SW1.2, U3.17 (PB2)
/stm32/MCU_RESET: C20.1, R8.1, RN3.5 (R4.2), U3.4 (NRST)
/stm32/Rx: RN4.1 (R1.1), U3.22 (PA10)
/stm32/SPI_MISO: RN1.3 (R3.1), U2.7 (SO)
/stm32/SPI_MOSI: RN1.4 (R4.1); also elsewhere on the board
/stm32/SPI_SCK: RN1.2 (R2.1), U2.5 (SCK); also elsewhere on the board
/stm32/SWCLK: RN3.7 (R2.2), U3.28 (PA14)
/stm32/SWDIO: RN3.8 (R1.2), U3.25 (PA13)
/stm32/SWO: RN3.6 (R3.2), U3.30 (PB3)
/stm32/Tx: RN4.4 (R4.1), U3.21 (PA9)
/stm32/~OLED_CS: RN2.8 (R1.2); also elsewhere on the board
/stm32/~OLED_RESET: RN2.7 (R2.2); also elsewhere on the board
GND: C1.2, C2.1, C3.1, C4.2, C17.2, C18.1, C19.2, C20.2, C21.2, C22.2, C23.2, C24.2, C25.2, D1.1 (K), D3.1 (K), D4.1 (K), J1.4, J1.6, R2.1, RV2.3, U2.1 (GND), U3.5 (VSSA), U3.18 (VSS), U3.26 (VSS), U3.36 (VSS), U3.37 (VSS), Y1.2, Y1.4; also elsewhere on the board
unnamed: C17.1, U3.3 (PD1), Y1.1
unnamed: C18.2, U3.2 (PD0), Y1.3
unnamed: D1.2 (A), R1.2
unnamed: D3.2 (A), R10.2
unnamed: D4.2 (A), R11.2
unnamed: H5.1, U2.3 (T+)
unnamed: H6.1, U2.2 (T-)
unnamed: J1.1, RN3.1 (R1.1)
unnamed: J1.3, RN3.2 (R2.1)
unnamed: J1.5, RN3.3 (R3.1)
unnamed: J1.8, RN4.8 (R1.2)
unnamed: J1.9, RN3.4 (R4.1)
unnamed: J1.10, RN4.5 (R4.2)
unnamed: R1.1, U3.31 (PB4)
unnamed: R9.2, U3.35 (BOOT0)
unnamed: R10.1, U3.32 (PB5)
unnamed: R11.1, U3.33 (PB6)
unnamed: RN1.1 (R1.1), U2.6 (~CS)
unnamed: RN1.5 (R4.2), U3.14 (PA7)
unnamed: RN1.6 (R3.2), U3.13 (PA6)
unnamed: RN1.7 (R2.2), U3.12 (PA5)
unnamed: RN1.8 (R1.2), U3.11 (PA4)
unnamed: RN2.1 (R1.1), U3.10 (PA3)
unnamed: RN2.2 (R2.1), U3.9 (PA2)
unnamed: RN2.3 (R3.1), U3.8 (PA1)
unnamed: RV2.2, U3.15 (PB0)

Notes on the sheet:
BOOT0 = 1 BOOT1 = 0 (PB2) Bootloader is on pb2, hold the btn while plugging in enables the bootloader
Supply Decoupling
STM32 Bootloader Activation
Hot Plate Reflow Soldering Controller Rev. 1
August 2019
T. Music

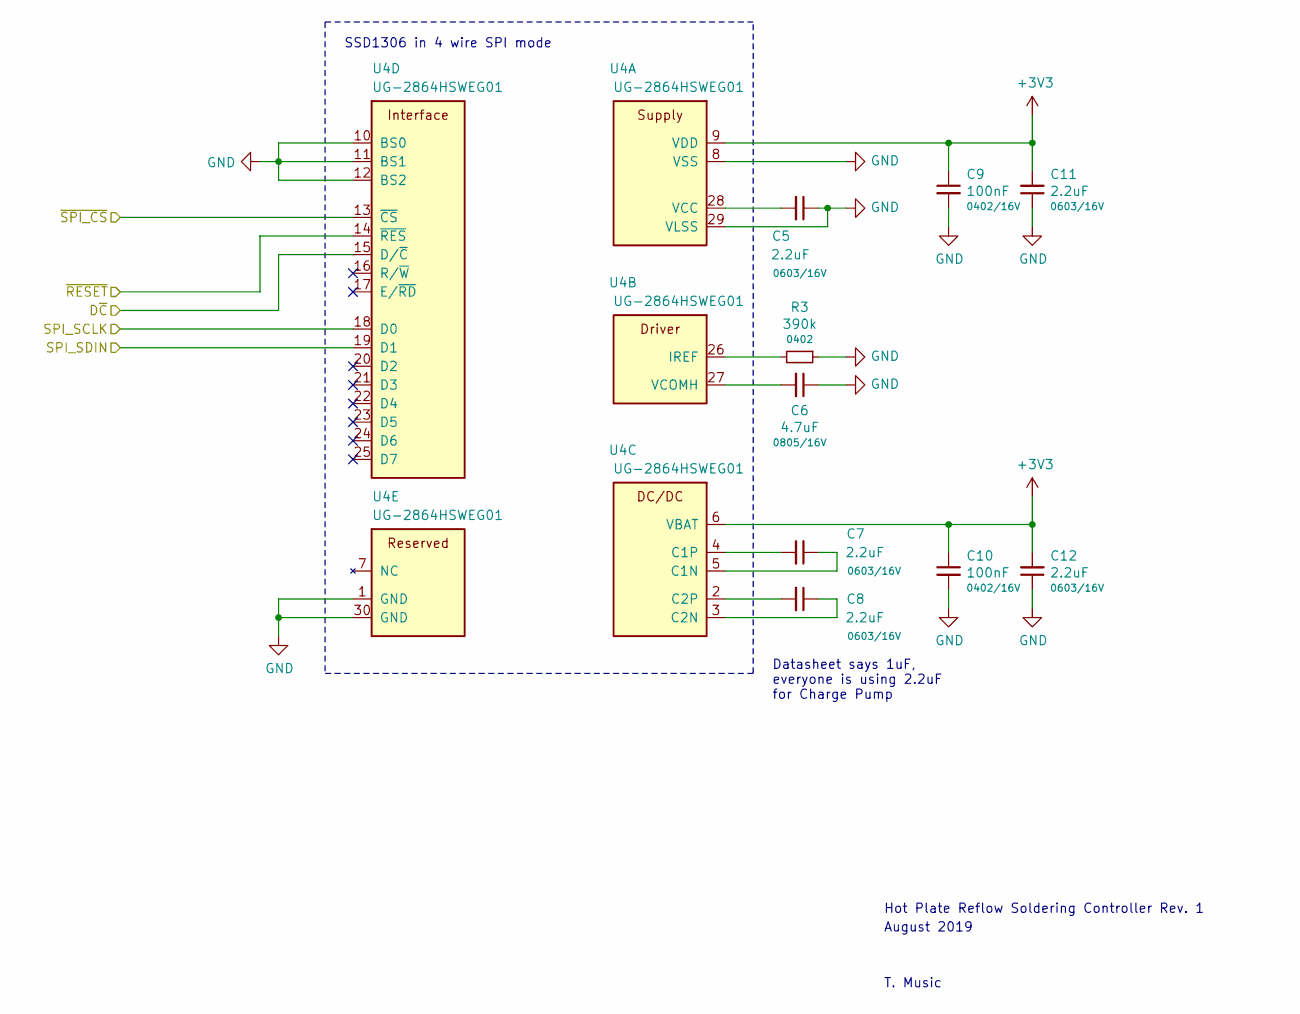
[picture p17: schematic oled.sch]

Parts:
C10, C31: 100nF; C_0402_1005Metric; Rating 0402/16V
C11, C12, C27, C29, C30: 2.2uF; C_0603_1608Metric; Rating 0603/16V; LCSC C23630
C28: 4.7uF; C_0805_2012Metric; Rating 0805/16V
R41: 390k; R_0402_1005Metric; Rating 0402
U9: UG-2864HSWEG01

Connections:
+3V3: C10.1, C11.2, C12.2; also elsewhere on the board
GND: C10.2, C11.1, C12.1; also elsewhere on the board

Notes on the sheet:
SSD1306 in 4 wire SPI mode
Datasheet says 1uF, everyone is using 2.2uF for Charge Pump
Hot Plate Reflow Soldering Controller Rev. 1
August 2019
T. Music

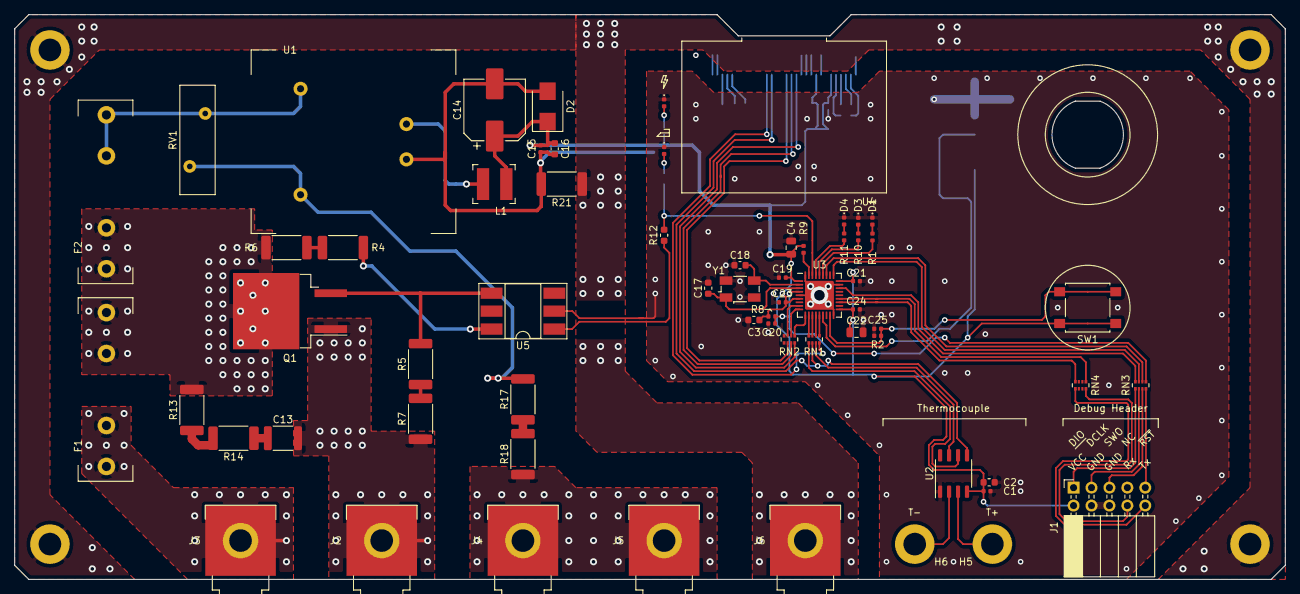
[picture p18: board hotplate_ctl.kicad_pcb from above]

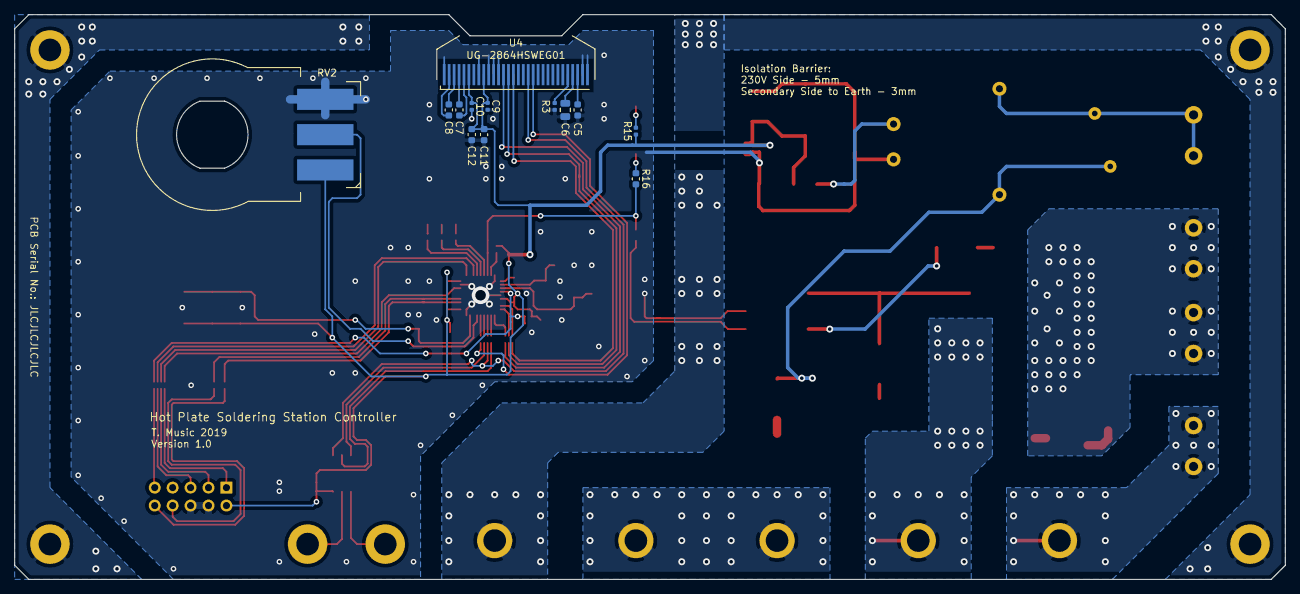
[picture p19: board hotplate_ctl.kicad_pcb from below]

Board: 2 copper layers, 180.0 x 80.0 mm, 79 parts (12 on the bottom side), 67 nets.

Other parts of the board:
C5, C7, C8: 2.2uF; C_0603_1608Metric
C6: 4.7uF; C_0805_2012Metric
C9: 100nF; C_0402_1005Metric
R3: 390k; R_0402_1005Metric
U4: UG-2864HSWEG01

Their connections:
+3V3: C9.1, U4.6, U4.9; also elsewhere on the board
/oled/D~C: U4.15; also elsewhere on the board
/stm32/SPI_MOSI: U4.19; also elsewhere on the board
/stm32/SPI_SCK: U4.18; also elsewhere on the board
/stm32/~OLED_CS: U4.13; also elsewhere on the board
/stm32/~OLED_RESET: U4.14; also elsewhere on the board
GND: C5.1, C6.1, C9.2, R3.1, U4.1, U4.8, U4.10, U4.11, U4.12, U4.29, U4.30; also elsewhere on the board
unnamed: C5.2, U4.28
unnamed: C6.2, U4.27
unnamed: C7.1, U4.5
unnamed: C7.2, U4.4
unnamed: C8.1, U4.3
unnamed: C8.2, U4.2
unnamed: R3.2, U4.26

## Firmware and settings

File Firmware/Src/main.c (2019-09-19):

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

/* Includes ------------------------------------------------------------------*/
#include "main.h"
#include "cmsis_os.h"

/* USER CODE BEGIN Includes */
#include "oled.h"
#include "pid.h"
#include "thermocouple.h"

/* USER CODE END Includes */

ADC_HandleTypeDef hadc1;

SPI_HandleTypeDef hspi1;

TIM_HandleTypeDef htim4;

UART_HandleTypeDef huart1;

osThreadId defaultTaskHandle;
uint32_t defaultTaskBuffer[ 128 ];
osStaticThreadDef_t defaultTaskControlBlock;
osThreadId pidTaskHandle;
uint32_t pidTaskBuffer[ 128 ];
osStaticThreadDef_t pidTaskControlBlock;
osThreadId tcTaskHandle;
uint32_t tcTaskBuffer[ 128 ];
osStaticThreadDef_t tcTaskControlBlock;
osThreadId controlTaskHandle;
uint32_t controlTaskBuffer[ 128 ];
osStaticThreadDef_t controlTaskControlBlock;
void SystemClock_Config(void);
static void MX_GPIO_Init(void);
static void MX_SPI1_Init(void);
static void MX_ADC1_Init(void);
static void MX_USART1_UART_Init(void);
static void MX_TIM4_Init(void);
void StartDefaultTask(void const * argument);
void StartPidTask(void const * argument);
void startTcTask(void const * argument);
extern void StartControlTask(void const * argument);

/* USER CODE BEGIN 0 */
  void vTaskLedRed(void *p) {
    for (;;) {
    }
  }

/* USER CODE END 0 */

/**
  * @brief  The application entry point.
  * @retval int
  */
int main(void)
{
  /* USER CODE BEGIN 1 */
  task_pid_status    = TASK_WAIT;
  task_pid_remaining = TASK_PID_INTERVAL;

  /* USER CODE END 1 */

  /* MCU Configuration--------------------------------------------------------*/

  /* Reset of all peripherals, Initializes the Flash interface and the Systick. */
  HAL_Init();

  /* Configure the system clock */
  SystemClock_Config();

  /* Initialize all configured peripherals */
  MX_GPIO_Init();
  MX_SPI1_Init();
  MX_ADC1_Init();
  MX_USART1_UART_Init();
  MX_TIM4_Init();
  /* USER CODE BEGIN 2 */
  HAL_GPIO_WritePin(OLED_CS_GPIO_Port, OLED_CS_Pin, GPIO_PIN_SET);
  HAL_GPIO_WritePin(TC_CS_GPIO_Port, TC_CS_Pin, GPIO_PIN_SET);
  oled_init();
  tc_init();

  //HAL_GPIO_WritePin(GPIOB, LED3_Pin, GPIO_PIN_SET);
  //HAL_GPIO_WritePin(GPIOB, LED2_Pin, GPIO_PIN_SET);
  //HAL_GPIO_WritePin(GPIOB, LED1_Pin, GPIO_PIN_SET);
 

  /* USER CODE END 2 */

  /* USER CODE BEGIN RTOS_MUTEX */
  /* add mutexes, ... */
  /* USER CODE END RTOS_MUTEX */

  /* USER CODE BEGIN RTOS_SEMAPHORES */
  /* add semaphores, ... */
  /* USER CODE END RTOS_SEMAPHORES */

  /* USER CODE BEGIN RTOS_TIMERS */
  /* start timers, add new ones, ... */
  /* USER CODE END RTOS_TIMERS */

  /* Create the thread(s) */
  /* definition and creation of defaultTask */
  osThreadStaticDef(defaultTask, StartDefaultTask, osPriorityNormal, 0, 128, defaultTaskBuffer, &defaultTaskControlBlock);
  defaultTaskHandle = osThreadCreate(osThread(defaultTask), NULL);

  /* definition and creation of pidTask */
  osThreadStaticDef(pidTask, StartPidTask, osPriorityAboveNormal, 0, 128, pidTaskBuffer, &pidTaskControlBlock);
  pidTaskHandle = osThreadCreate(osThread(pidTask), NULL);

  /* definition and creation of tcTask */
  osThreadStaticDef(tcTask, startTcTask, osPriorityNormal, 0, 128, tcTaskBuffer, &tcTaskControlBlock);
  tcTaskHandle = osThreadCreate(osThread(tcTask), NULL);

  /* definition and creation of controlTask */
  osThreadStaticDef(controlTask, StartControlTask, osPriorityNormal, 0, 128, controlTaskBuffer, &controlTaskControlBlock);
  controlTaskHandle = osThreadCreate(osThread(controlTask), NULL);

  /* USER CODE BEGIN RTOS_THREADS */
  /* add threads, ... */
  /* USER CODE END RTOS_THREADS */

  /* USER CODE BEGIN RTOS_QUEUES */
  /* add queues, ... */
  /* USER CODE END RTOS_QUEUES */

  /* Start scheduler */
  osKernelStart();

  /* We should never get here as control is now taken by the scheduler */

  /* Infinite loop */
  /* USER CODE BEGIN WHILE */
  while (1)
  {
    /* USER CODE END WHILE */

    /* USER CODE BEGIN 3 */
  }
  /* USER CODE END 3 */
}

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
/* USER CODE BEGIN Header_StartDefaultTask */
/**
  * @brief  Function implementing the defaultTask thread.
  * @param  argument: Not used 
  * @retval None
  */
/* USER CODE END Header_StartDefaultTask */
void StartDefaultTask(void const * argument)
{

  /* USER CODE BEGIN 5 */
   TickType_t xLastWakeTime;
   const TickType_t xFrequency = 100;
   // Initialise the xLastWakeTime variable with the current time.
   xLastWakeTime = xTaskGetTickCount();

  /* Infinite loop */
  for(;;)
  {
      osDelay(100);
      /*
      uint8_t cbuf[8];
      char displaybuf[24];
      uint16_t temp = tc_getAverageTemperature();
      uint32_t ctime = HAL_GetTick();
      cbuf[0] = (ctime >> 24) & 0xFF;
      cbuf[1] = (ctime >> 16) & 0xFF;
      cbuf[2] = (ctime >> 8) & 0xFF;
      cbuf[3] = (ctime & 0xFF);
      uint8_t t_msb = temp >> 8;
      cbuf[4] = t_msb & 0xFF; //(char) (temp >> 8) & 0xFF;
      cbuf[5] = temp & 0xFF;
      cbuf[6] = pid_getCurOutputPower() & 0xFF;
      cbuf[7] = '\n';

      HAL_UART_Transmit(&huart1, &cbuf, 8, HAL_MAX_DELAY);

      u8g2_ClearBuffer(&u8g2);
      u8g2_SetFont(&u8g2, u8g2_font_helvB10_tr);

      uint16_t fracTemp = temp;
      temp /= 100;
      fracTemp -= temp * 100;
      sprintf(displaybuf, "%d.%d C - %d %%", temp, fracTemp, pid_getCurOutputPower());
      u8g2_DrawStr(&u8g2, 0, 64, displaybuf);

      uint32_t aval = 0;

      HAL_ADC_Start(&hadc1);
      if (HAL_ADC_PollForConversion(&hadc1, 1000000) == HAL_OK) {
        aval = HAL_ADC_GetValue(&hadc1);
      }

      if (aval > 2000 && pid_getStatus() == 0)
          pid_enable();

      if (aval < 1000 && pid_getStatus() == 1)
          pid_disable();

      sprintf(displaybuf, "%d", aval);
      u8g2_DrawStr(&u8g2, 0, 32, displaybuf);

      if (pid_getStatus() == 0)
        u8g2_DrawStr(&u8g2, 40, 15, "PID off");
      else
        u8g2_DrawStr(&u8g2, 40, 15, "PID on");


      u8g2_SendBuffer(&u8g2);

      vTaskDelayUntil( &xLastWakeTime, xFrequency );
*/
      //osDelay(1000);
  }
  /* USER CODE END 5 */ 
}

/* USER CODE BEGIN Header_StartPidTask */
/**
* @brief Function implementing the pidTask thread.
* @param argument: Not used
* @retval None
*/
/* USER CODE END Header_StartPidTask */
void StartPidTask(void const * argument)
{
  /* USER CODE BEGIN StartPidTask */
   TickType_t xLastWakeTime;
   const TickType_t xFrequency = 100;
   // Initialise the xLastWakeTime variable with the current time.
   xLastWakeTime = xTaskGetTickCount();

   pid_init();
   __HAL_TIM_SET_COMPARE(&htim4, TIM_CHANNEL_2, 0);
   HAL_TIM_PWM_Start(&htim4, TIM_CHANNEL_2);

  /* Infinite loop */
  for(;;)
  {
      uint16_t power = pid_calculate();
      power *= 80;
      __HAL_TIM_SET_COMPARE(&htim4, TIM_CHANNEL_2, power);
      vTaskDelayUntil(&xLastWakeTime, xFrequency);
  }
  /* USER CODE END StartPidTask */
}

/* USER CODE BEGIN Header_startTcTask */
/**
* @brief Function implementing the tcTask thread.
* @param argument: Not used
* @retval None
*/
/* USER CODE END Header_startTcTask */
void startTcTask(void const * argument)
{
  /* USER CODE BEGIN startTcTask */
  TickType_t xLastWakeTime;
  const TickType_t xFrequency = 25;
  // Initialise the xLastWakeTime variable with the current time.
  xLastWakeTime = xTaskGetTickCount();

  /* Infinite loop */
  for(;;)
  {
    tc_poll();
    vTaskDelayUntil(&xLastWakeTime, xFrequency);
  }
  /* USER CODE END startTcTask */
}

/**
  * @brief  Period elapsed callback in non blocking mode
  * @note   This function is called  when TIM1 interrupt took place, inside
  * HAL_TIM_IRQHandler(). It makes a direct call to HAL_IncTick() to increment
  * a global variable "uwTick" used as application time base.
  * @param  htim : TIM handle
  * @retval None
  */
void HAL_TIM_PeriodElapsedCallback(TIM_HandleTypeDef *htim)
{
  if (htim->Instance == TIM1) {
    HAL_IncTick();
  }
}

/**
  * @brief  This function is executed in case of error occurrence.
  * @retval None
  */
void Error_Handler(void)
{
  /* USER CODE BEGIN Error_Handler_Debug */
  /* User can add his own implementation to report the HAL error return state */

  /* USER CODE END Error_Handler_Debug */
}

#ifdef  USE_FULL_ASSERT
/**
  * @brief  Reports the name of the source file and the source line number
  *         where the assert_param error has occurred.
  * @param  file: pointer to the source file name
  * @param  line: assert_param error line source number
  * @retval None
  */
void assert_failed(uint8_t *file, uint32_t line)
{ 
  /* USER CODE BEGIN 6 */
  /* User can add his own implementation to report the file name and line number,
     tex: printf("Wrong parameters value: file %s on line %d\r\n", file, line) */
  /* USER CODE END 6 */
}
#endif /* USE_FULL_ASSERT */

/************************ (C) COPYRIGHT STMicroelectronics *****END OF FILE****/

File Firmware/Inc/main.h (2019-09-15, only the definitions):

#define OLED_DC_Pin GPIO_PIN_1
#define OLED_DC_GPIO_Port GPIOA
#define OLED_RESET_Pin GPIO_PIN_2
#define OLED_RESET_GPIO_Port GPIOA
#define OLED_CS_Pin GPIO_PIN_3
#define OLED_CS_GPIO_Port GPIOA
#define TC_CS_Pin GPIO_PIN_4
#define TC_CS_GPIO_Port GPIOA
#define POTI_ADC_Pin GPIO_PIN_0
#define POTI_ADC_GPIO_Port GPIOB
#define BTN_START_Pin GPIO_PIN_2
#define BTN_START_GPIO_Port GPIOB
#define LED1_Pin GPIO_PIN_4
#define LED1_GPIO_Port GPIOB
#define LED2_Pin GPIO_PIN_5
#define LED2_GPIO_Port GPIOB
#define LED3_Pin GPIO_PIN_6
#define LED3_GPIO_Port GPIOB
#define IRON_CTL_Pin GPIO_PIN_7
#define IRON_CTL_GPIO_Port GPIOB
#define TASK_RUN  1
#define TASK_WAIT 0
#define TASK_PID_INTERVAL 500

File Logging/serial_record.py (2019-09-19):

#!/usr/bin/env python

# Script to record all measurements from the Iron

import serial
import os
import numpy as np
#import matplotlib.pyplot as plt
from datetime import datetime

import Gnuplot

ser = serial.Serial('/dev/ttyUSB1', 115200, timeout=0.2)

logfile = open("templog_{}.csv".format(datetime.now().strftime("%Y%m%d_%H%M%S")),"a+")
last_temp = -1

entry_found = False

ki = 0
kp = 0
kd = 0

print("Waiting for start")

while entry_found == False:
    try:
        line = ser.read(13)
        #print(line)
        if line[0] != 0xAA: ## If the frame does not start with 0xAA -> discard
          continue

        entry_found = True
        kp = int.from_bytes(line[1:5],  byteorder='big') / 1000
        ki = int.from_bytes(line[5:9],  byteorder='big') / 1000
        kd = int.from_bytes(line[9:13], byteorder='big') / 1000
        print("Kp: {:.3f} Ki: {:.3f} Kd: {:.3f}".format(kp, ki, kd))
        logfile.write("# Kp: {:.3f} Ki: {:.3f} Kd: {:.3f}".format(kp, ki, kd))

    except KeyboardInterrupt:
        break
    except:
        #print("Invalid frame received, skipping " + str(line))
        continue

print("Start found")

while True:
    try:
        line = ser.read(8)
        #print(line)
        if line[0] != 0xAB: ## If the frame does not start with 0xAB -> discard
          continue
        ctime = int.from_bytes(line[1:3], byteorder='big')
        ttemp = int.from_bytes(line[3:5], byteorder='big')
        ctemp = int.from_bytes(line[5:7], byteorder='big')
        cpwr  = line[7]
        ctime = ctime / 10
        ctemp = ctemp / 100
        ttemp = ttemp / 10
        if last_temp == -1:
            last_temp = ctemp
        tdelta = (ctemp - last_temp) * 50
        #logfile.write("%.1f;%.1f;%.2f;%.2f;%d\n" % (ctime, ttemp, ctemp, tdelta, cpwr))
        logfile.write("%.1f;%.1f;%.2f;%.2f;%d;%.2f\n" % (ctime, ttemp, ctemp, tdelta, cpwr, ttemp - ctemp))
        print("{:8.1f}  -  Target {:5.1f} °C  -  Ist {:6.2f} °C  -  Abweichung {:7.2f} °C  -  Delta {:5.2f} d°C/s  -  P {:3d} %".format(ctime, ttemp, ctemp, ttemp - ctemp, ctemp - last_temp, cpwr))
        last_temp = ctemp
    except KeyboardInterrupt:
        break
    except:
        #print("Invalid frame received, skipping " + str(line))
        continue

logfile.close()

gp = Gnuplot.Gnuplot()

gp.load("pid.gp")
gp.set_string("out", os.path.splitext(logfile.name)[0] + ".pdf")
gp.set_string("title", "Temperature Curve Measurement "   +
              datetime.now().strftime("%H:%M - %d.%m.%Y") +
              " k_p: {:.3f} k_i: {:.3f} k_d: {:.3f}".format(kp, ki, kd))
gp.plot("\'{}\' using 1:2 title \'Target Temperature [°C]\' with lines,\
         \'{}\' using 1:3 title \'Iron Temperature [°C]\' with lines,\
         \'{}\' using 1:4 title \'DTemperature [°C/10]\' with lines,\
         \'{}\' using 1:6 title \'Error [°C]\' with lines,\
         \'{}\' using 1:5 title \'Heating [%]\' with lines,\
         ".format(logfile.name, logfile.name, logfile.name, logfile.name, logfile.name))

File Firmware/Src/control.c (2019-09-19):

#include "control.h"
#include "main.h"
#include "cmsis_os.h"
#include "pid.h"
#include "thermocouple.h"
#include "oled.h"

extern UART_HandleTypeDef huart1;
extern ADC_HandleTypeDef hadc1;


// State Machine

#define STATE_IDLE 0
#define STATE_HEAT 1
#define STATE_COOL 2
#define STATE_SETTINGS 3

volatile uint8_t state;

// Time elapsed in 1/10s
volatile uint16_t sTime;
volatile uint8_t  uBuffer[32];
volatile uint8_t btnStateOld;
volatile uint8_t btnState;
volatile uint32_t aval;

void StartControlTask(void const * argument) {

    state = STATE_IDLE;

    TickType_t xLastWakeTime;
    const TickType_t xFrequency = 20; // 20 Ticks is 200 ms
    xLastWakeTime = xTaskGetTickCount();

    char displaybuf[32];
    uint32_t kp, ki, kd;
    uint16_t temp, fracTemp;
    uint8_t setpointIndex;

    int32_t pidErrorOld;
    int32_t pidError;

    btnStateOld = 0;
    uint32_t delaycount;

    // If continue is used -> no sleep
    // If break is used -> delay routine kicks in

    while(1) {
        //HAL_GPIO_WritePin(GPIOB, LED3_Pin, GPIO_PIN_SET);

        switch(state) {
            case STATE_IDLE:
                u8g2_ClearBuffer(&u8g2);
                u8g2_SetFont(&u8g2, u8g2_font_helvB10_tr);
                u8g2_DrawStr(&u8g2, 55, 15, "Idle");
                temp = tc_getAverageTemperature();
                fracTemp = temp;
                temp /= 100;
                fracTemp -= temp * 100;
                sprintf(displaybuf, "CTemp %d.%d C", temp, fracTemp);
                u8g2_DrawStr(&u8g2, 0, 30, displaybuf);
                u8g2_SendBuffer(&u8g2);

                btnState = HAL_GPIO_ReadPin(BTN_START_GPIO_Port,BTN_START_Pin);
                if ( btnState == btnStateOld )
                    break;

                if ( btnStateOld == 0 && btnState == 1 ) {
                    btnStateOld = btnState;
                    break;
                }

                btnStateOld = btnState;

                kp = pid_getKp();
                ki = pid_getKi();
                kd = pid_getKd();

                uBuffer[0]  = 0xAA; // ID -> Is temperature log start
                uBuffer[1]  = (kp >> 24) & 0xFF;
                uBuffer[2]  = (kp >> 16) & 0xFF;
                uBuffer[3]  = (kp >> 8) & 0xFF;
                uBuffer[4]  =  kp & 0xFF;
                uBuffer[5]  = (ki >> 24) & 0xFF;
                uBuffer[6]  = (ki >> 16) & 0xFF;
                uBuffer[7]  = (ki >> 8) & 0xFF;
                uBuffer[8]  =  ki & 0xFF;
                uBuffer[9]  = (kd >> 24) & 0xFF;
                uBuffer[10] = (kd >> 16) & 0xFF;
                uBuffer[11] = (kd >> 8) & 0xFF;
                uBuffer[12] =  kd & 0xFF;
                HAL_UART_Transmit_IT(&huart1, &uBuffer, 13);

                // Before switching to heat initialise the solder timer
                sTime = 0;
                setpointIndex = 0;
                pidErrorOld = 0;
                delaycount = 600;
                pid_setTargetTemperature(tc_getAverageTemperature()/10);
                state = STATE_HEAT;
                pid_enable();
            break;

            case STATE_HEAT:
                HAL_ADC_Start(&hadc1);
                if (HAL_ADC_PollForConversion(&hadc1, 1000000) == HAL_OK) {
                    aval = HAL_ADC_GetValue(&hadc1);
                }

                if (aval < 2000) {
                    pid_disable();
                    state = STATE_IDLE;
                    break;
                }

                // If needed adjust PID
                if ( (sTime % 10) == 0 ) {
                    uint16_t cSec = sTime / 10;
                    // If there is a temperature for the current time apply it
                    if ( cSec < (sizeof(tempProfile) / sizeof(tempProfile[0])) ) {
                        pid_setTargetTemperature(tempProfile[cSec]);
                    } else {
                        pid_disable();
                        state = STATE_IDLE;
                        break;
                    }
                    HAL_GPIO_TogglePin(GPIOB, LED2_Pin);
                }


                /*pidError = pid_getCurError();
                delaycount++;
                if ( (pidError != pidErrorOld) && (pidError < 0) && (delaycount > 149)) {
                    pidErrorOld = pidError;
                    pid_setTargetTemperature(pid_getTargetTemperature() + 500);
                    delaycount = 0;
                }*/

                // Log values
                uBuffer[0] = 0xAB; // ID -> Is temperature log
                uBuffer[1] = (sTime >> 8) & 0xFF;
                uBuffer[2] = sTime & 0xFF;
                temp = pid_getTargetTemperature();
                uBuffer[3] = (temp >> 8) & 0xFF;
                uBuffer[4] = temp & 0xFF;
                temp = tc_getAverageTemperature();
                uBuffer[5] = (temp >> 8) & 0xFF;
                uBuffer[6] = temp & 0xFF;
                uBuffer[7] = pid_getCurOutputPower() & 0xFF;

                HAL_UART_Transmit_IT(&huart1, &uBuffer, 8);

                // OLED
                u8g2_ClearBuffer(&u8g2);
                u8g2_SetFont(&u8g2, u8g2_font_helvB10_tr);
                temp = tc_getAverageTemperature();
                fracTemp = temp;
                temp /= 100;
                fracTemp -= temp * 100;
                sprintf(displaybuf, "CTemp %d.%d C", temp, fracTemp);
                u8g2_DrawStr(&u8g2, 0, 15, displaybuf);

                // Display Target Temperature
                temp = pid_getTargetTemperature();
                fracTemp = temp;
                temp /= 10;
                fracTemp -= temp * 10;
                sprintf(displaybuf, "TTemp %d.%d C", temp, fracTemp);
                u8g2_DrawStr(&u8g2, 0, 30, displaybuf);

                //sprintf(displaybuf, "%d.%d C - %d %%", temp, fracTemp, pid_getCurOutputPower());
                sprintf(displaybuf, "Time %d", sTime);
                u8g2_DrawStr(&u8g2, 0, 45, displaybuf);
                u8g2_SendBuffer(&u8g2);

                sprintf(displaybuf, "Power %d %%", pid_getCurOutputPower());
                u8g2_DrawStr(&u8g2, 0, 64, displaybuf);
                u8g2_SendBuffer(&u8g2);

                sTime += 2; // Add 200 ms to the timer
            break;

            default:
                // If an illegal state would occur, revert back to idle
                state = STATE_IDLE;
                pid_disable();
        }

        //HAL_GPIO_WritePin(GPIOB, LED3_Pin, GPIO_PIN_RESET);
        vTaskDelayUntil( &xLastWakeTime, xFrequency );
    }

    return;
}
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

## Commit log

2019-08-30 First commit. Added images, preliminary readme, gitignore and license
    [hotplate_ctl-B_Cu.gbr, hotplate_ctl-B_Mask.gbr, hotplate_ctl-B_SilkS.gbr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]
2019-08-30 Added KiCAD files of rev1
    [hotplate_ctl.kicad_pcb, hotplate_ctl.sch, oled.sch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]
2019-09-15 SW WIP, regulator does not respond well to predefined curve from table
2019-09-19 Coarse simulation of the hot plate
2019-09-19 Added interactive BOM
2019-09-19 Added Makefile and STM32CubeMX configs
2019-09-19 Made PCB view prettier
2019-09-19 Added python logging and plotting script
    [templog_20190915_155821.csv, templog_20190916_003306.csv]
2019-09-19 Drivers from ST and U8G2 lib are not in the repo
2019-09-19 Added temperature logs to gitignore

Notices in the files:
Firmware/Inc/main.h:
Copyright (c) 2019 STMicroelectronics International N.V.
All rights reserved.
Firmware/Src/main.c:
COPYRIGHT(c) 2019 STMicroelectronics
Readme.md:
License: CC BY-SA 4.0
